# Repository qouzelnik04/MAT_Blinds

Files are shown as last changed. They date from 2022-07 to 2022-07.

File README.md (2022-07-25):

# MAT_Blinds

## Introduction
- hardware has revision (rev)
- software has version (ver)

Fully automatic blinds with the possibility of manual control. They allow setting the position of the blind, the pull up / pull down time. User interface with display and buttons. 
- constantly evolving project
- works with "day and night" blinds
- based on STM32
- whole instructions in the documentation

## News
Work is underway on [rev_2.0](./Schematic/rev_2.0/README.md), which should be released during July 2022.

features [rev_2.0](./Schematic/rev_2.0/README.md)
- custom PCB
    - universal PCB
- encoder/buttons
- support [ver_2.0](./Code/ver_2.0/README.md)
    - English menu
    - Encoder

## Video
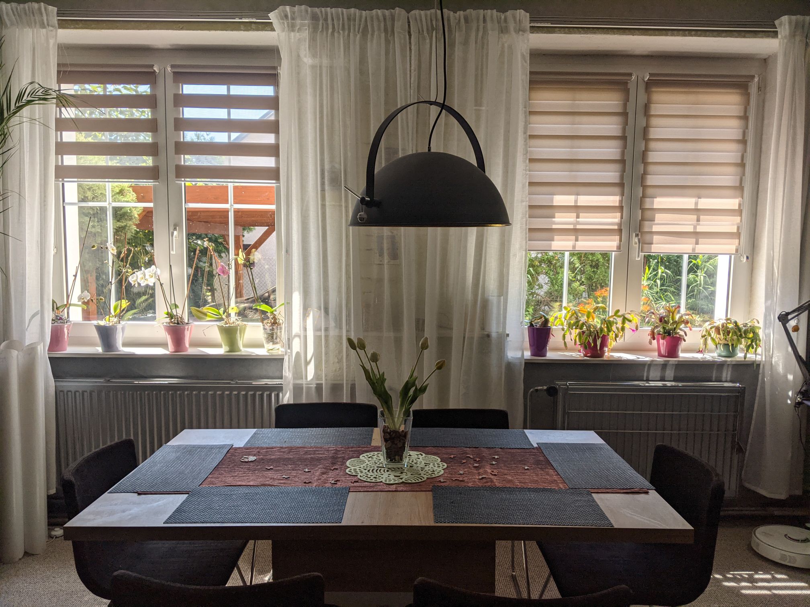
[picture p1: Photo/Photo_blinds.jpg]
(https://youtube.com/shorts/5kGoCTF1azA "Click to Watch!")

Click to Watch! ([rev_3.0](./Schematic/rev_3.0/) with [ver_3.0](./Code/ver_3.0/))

## Present
[rev_3.0](./Schematic/rev_3.0/) currently works with software [ver_3.0](./Code/ver_3.0/)

## Future improve
- release [rev_2.0](./Schematic/rev_2.0/README.md)
- release [ver_2.0](./Code/ver_2.0/README.md)
- lights sensors
- google assistant support

## Documentation
- [Instructions](./explanations/instructions.md)
- [Scheamtic](./Schematic/)
- [Code](./Code/)
- [Photo](./Photo/)

## License
Licensed under the [MIT License](./LICENSE)

## Author
- [@qouzelnik04](https://www.github.com/qouzelnik04)

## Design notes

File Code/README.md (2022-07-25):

# Software

## Introduction
- hardware has revision ([rev](../Schematic/README.md))
- software has version ([ver](./README.md))

For each software version, it is written which board revision it supports. This must be observed.
Each version of the software has detailed specifications of what it supports in the "README.md" file.

The software versions, their advantages and disadvantages are listed below.

## Actual version
### [ver_1.1](./ver_1.1/README.md) (not recommended)
- advantages
    - support 6 blinds
    - automatic pulling up and pulling down
- disadvantages
    - Required knowledge of STM32Cube to calibrate the blind.
    - support only Czech

### [ver_3.0](./ver_3.0/README.md) (recommended)
- advantages
    - easy to build (support [rev_3.0](../Schematic/rev_3.0/README.md))
    - support 4 blinds
    - automatic pulling up and pulling down
    - Supports English and Czech languages.

## Coming Soon
### [ver_2.0](./ver_2.0/README.md)
- advantages
    - Supports English and Czech languages.
    - support 6 blinds
    - automatic pulling up and pulling down
    - ...

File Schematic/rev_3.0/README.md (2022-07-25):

# rev_3.0 

## Introduction
rev_3.0 is the hardware part of the MAT_Blinds project. It was launched during July 2022 and replaced [rev_1.0](../rev_1.0/README.md).

- Easy to build
- Supports software versions only from 3.0 ([ver_3.0](../../Code/ver_3.0/README.md))
- Up to 4 blinds (4 motors)
- 1.3" display with encoder 

## Parts
- NUCLEO-F411RE (MCU)
- Arduino CNC shield
- 4x A4988 (Stepper Motor Driver)
- SSH1106 (1.3" OLED display)
- Encoder
- Power supply (9V 1A)
- [Case](../../parts/3D_parts/Case_rev_3.0.obj) Big a shout-out to [my brother](https://www.instagram.com/matalan09/?theme=dark) for designing these proposals.

- [How to make rev_3.0 board](./How_to_make_board.md)

## Photo
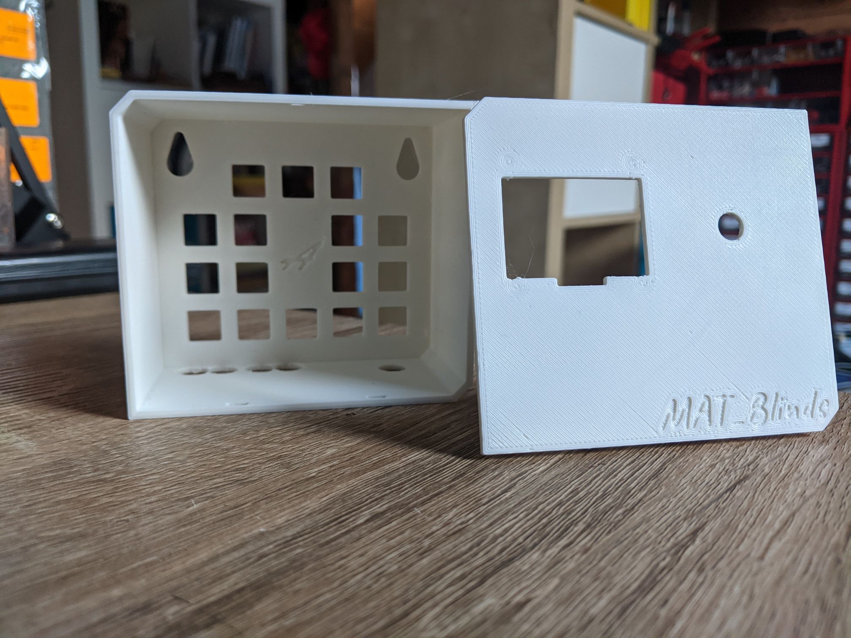
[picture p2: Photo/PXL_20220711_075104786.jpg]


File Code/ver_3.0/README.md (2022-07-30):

# ver_3.0 

## Introduction
ver_3.0 is the software part of the MAT_Blinds project. It was launched during July 2022 and replaced [ver_1.0](../ver_1.0/README.md).

- Supports hardware versions only 3.0 ([rev_3.0](..//../Schematic/rev_3.0/README.md))
- Supports English and Czech languages.
- easy to build (support [rev_3.0](../Schematic/rev_3.0/README.md))
- up to 4 blinds (4 motors)
    - the blinds are pulling up / pulling down at the same time
    - [separate control](../../explanations/separate_control.md)   
- 1.3" display with Encoder

### Update for version 3.1
- ver_3.1
    - code optimization
    - larger range of blinds
    - greater accuracy of blinds
    - add display shutdown after 30s of non-use

Here is [Setup](Setup.md) 

## Video
(https://youtube.com/shorts/5kGoCTF1azA "Click to Watch!")
Click to Watch! ([rev_3.0](./Schematic/rev_3.0/) with [ver_3.0](./Code/ver_3.0/))

## Photo
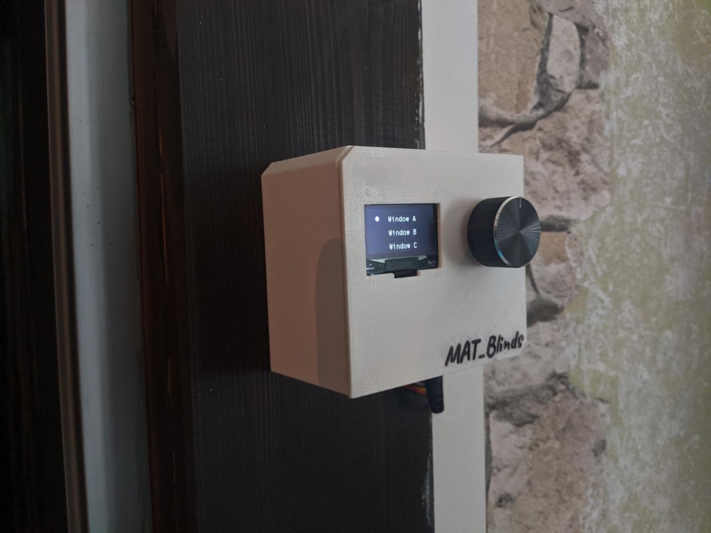
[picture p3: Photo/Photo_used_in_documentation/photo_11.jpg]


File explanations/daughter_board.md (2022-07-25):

# Daughter board

## Introduction
An explanation of what "daughter board" means.

Daughter boards are printed circuit boards with a required chip mounted on them with few other hardware components. 
## Examples of photos
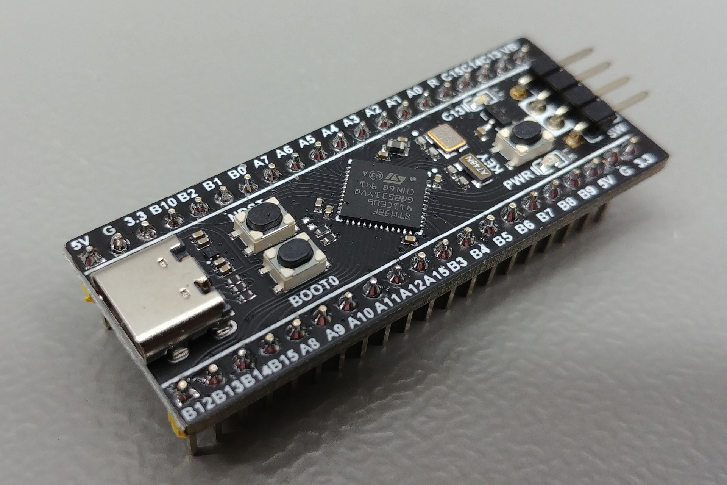
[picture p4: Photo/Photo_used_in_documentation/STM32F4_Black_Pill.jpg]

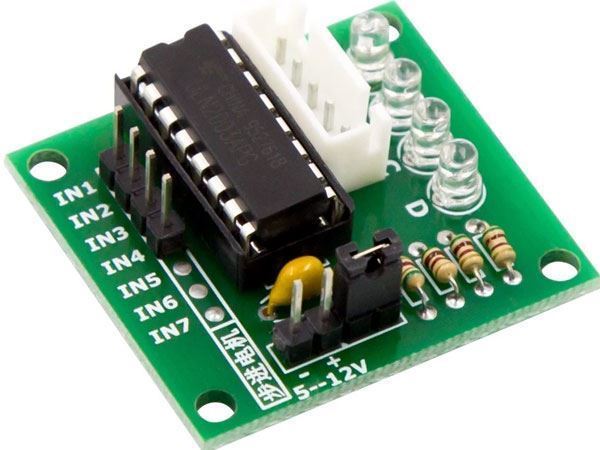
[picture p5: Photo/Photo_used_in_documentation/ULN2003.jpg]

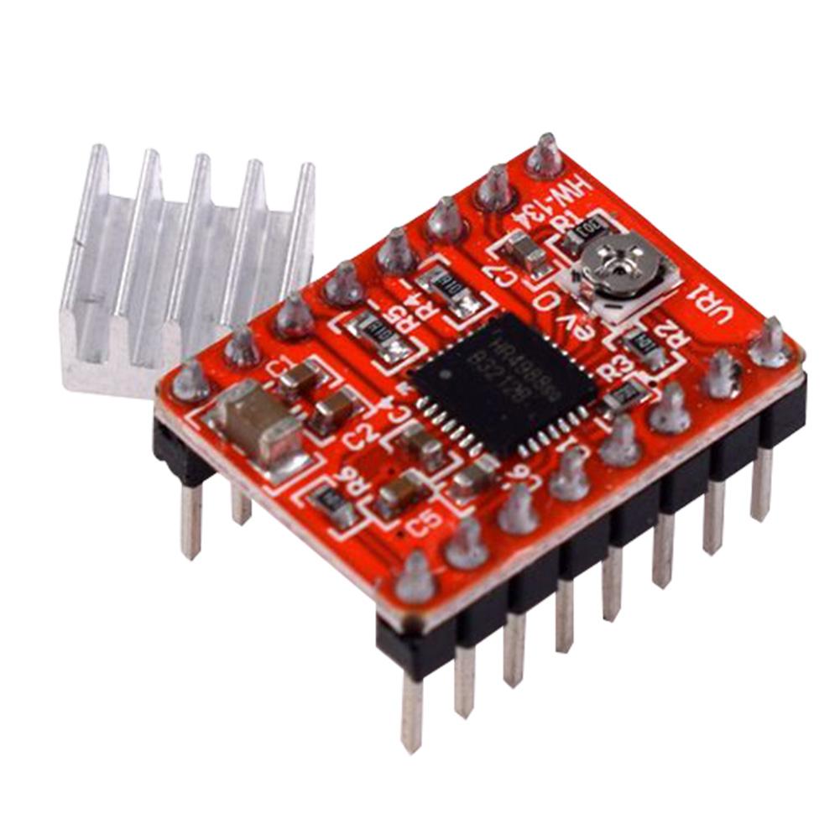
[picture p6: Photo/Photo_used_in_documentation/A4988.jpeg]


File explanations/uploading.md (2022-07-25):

# Uploading

## STM32 ST-LINK utility
### requirements 
- ST Link (if you have [revision 3.0](../Schematic/rev_3.0/)) it already has ST-Link built into it.
- [STM32 ST-LINK utility](https://www.st.com/en/development-tools/stsw-link004.html#get-software)

After downloading the STM32 ST-LINK utility and opening it, you will get [here](../Photo/Photo_used_in_documentation/ST_LINK_utility_3.png).

Now we connect the board to the computer. 
- If we have revision 3.0, it will be much easier, we will only need a mini USB cable.
- If we have revision 1.0, dirstly we will need to connect the board to ST-Link and ST-Link to the computer. [As in the picture](../Photo/Photo_used_in_documentation/ST_LINK_utility_4.jpg)
    - yellow - SWDIO
    - blue - GND
    - green - SWCLK
    - orange -3.3V
- Now we will download the software. In the folder of the software version we want to use, there is a file called ver_x.x.hex, for example (ver_3.0.hex). We'll download it.
- Now we connect the board in the STM32 ST-Link utility, by clicking on the "Connect to the target" button. If the board connects successfully, below we see the name of the board and it is connected. [As in the picture](../Photo/Photo_used_in_documentation/ST_LINK_utility_5.png)
- Now drag the downloaded .hex file into the STM32 ST-Link utility and click on "Program verify" then click on start. Then it should write something similar to the [picture](../Photo/Photo_used_in_documentation/ST_LINK_utility_7.png)
- Now the software is uploaded, all we have to do is disconnect from the device by clicking "Disconnect form the target" [As in the picture](../Photo/Photo_used_in_documentation/ST_LINK_utility_9.png)

### Photo

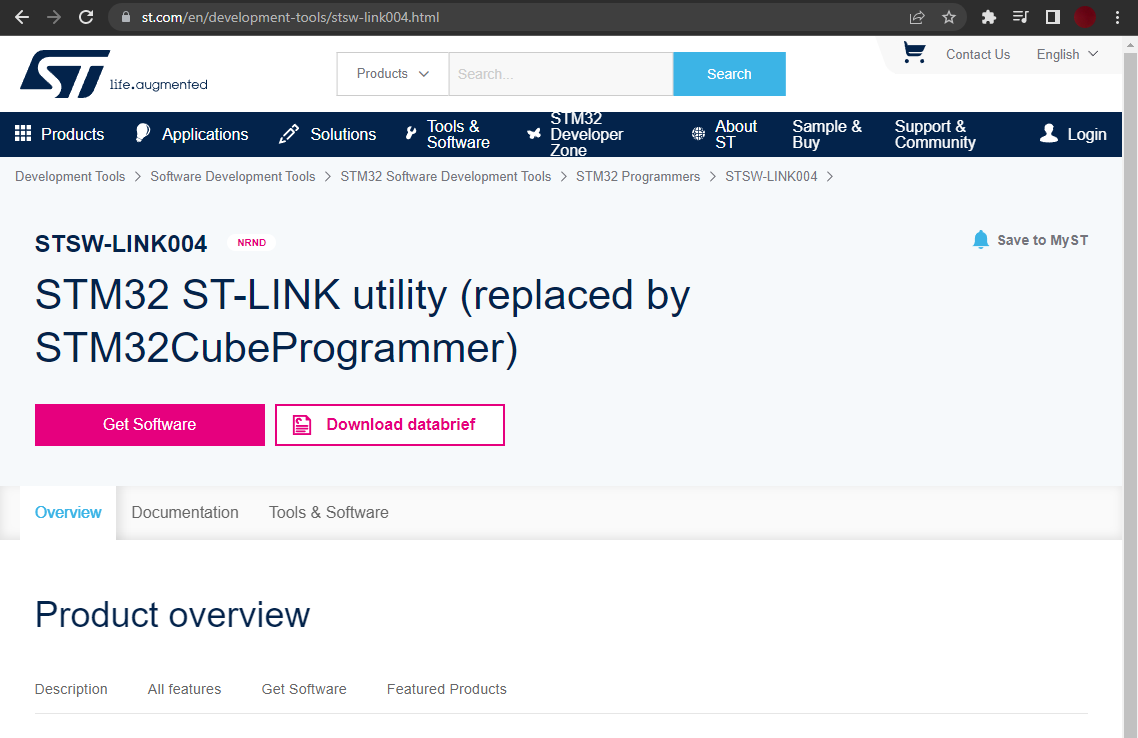
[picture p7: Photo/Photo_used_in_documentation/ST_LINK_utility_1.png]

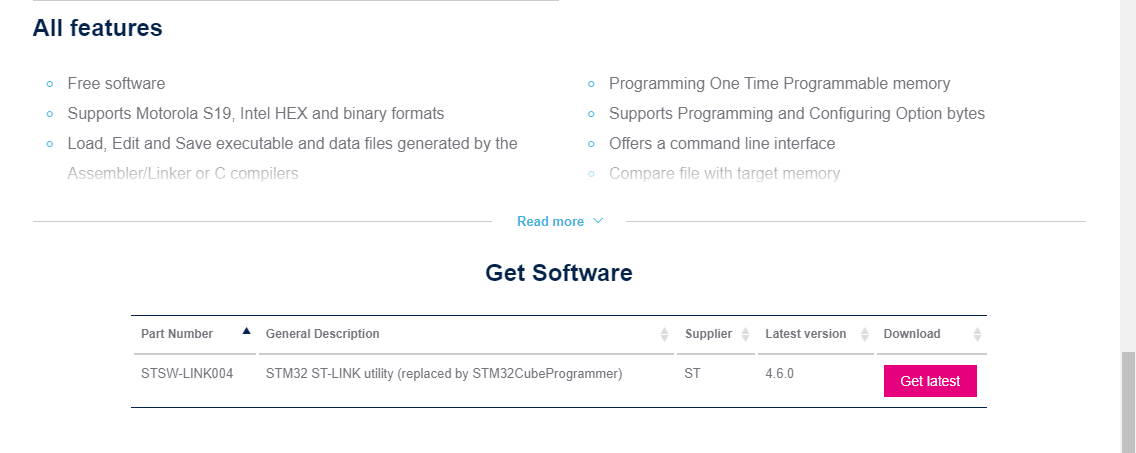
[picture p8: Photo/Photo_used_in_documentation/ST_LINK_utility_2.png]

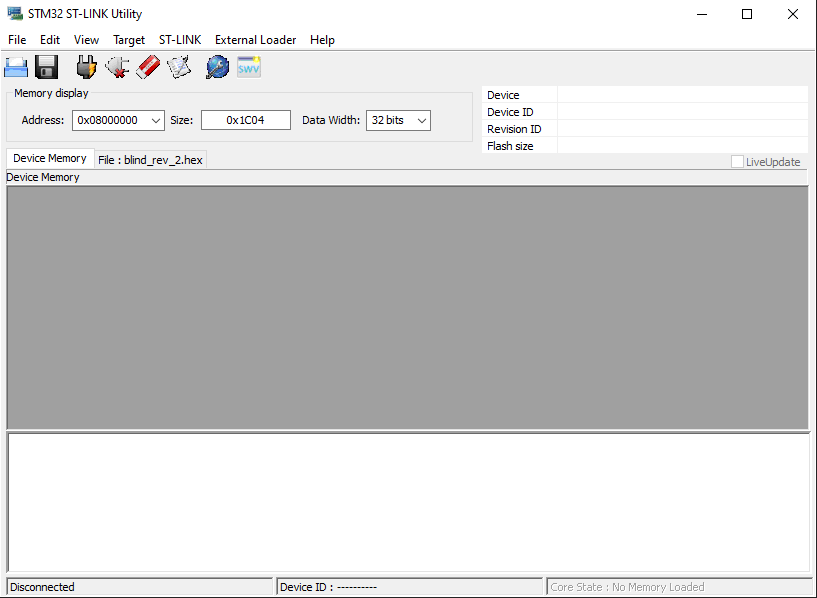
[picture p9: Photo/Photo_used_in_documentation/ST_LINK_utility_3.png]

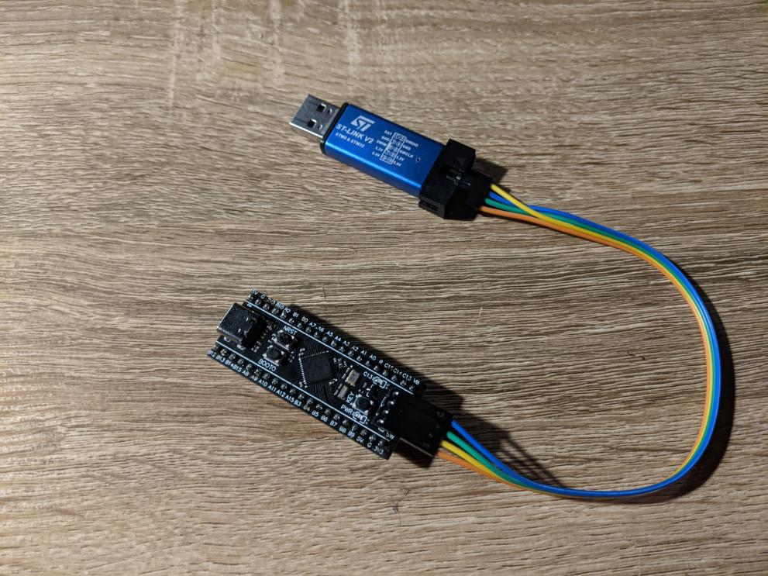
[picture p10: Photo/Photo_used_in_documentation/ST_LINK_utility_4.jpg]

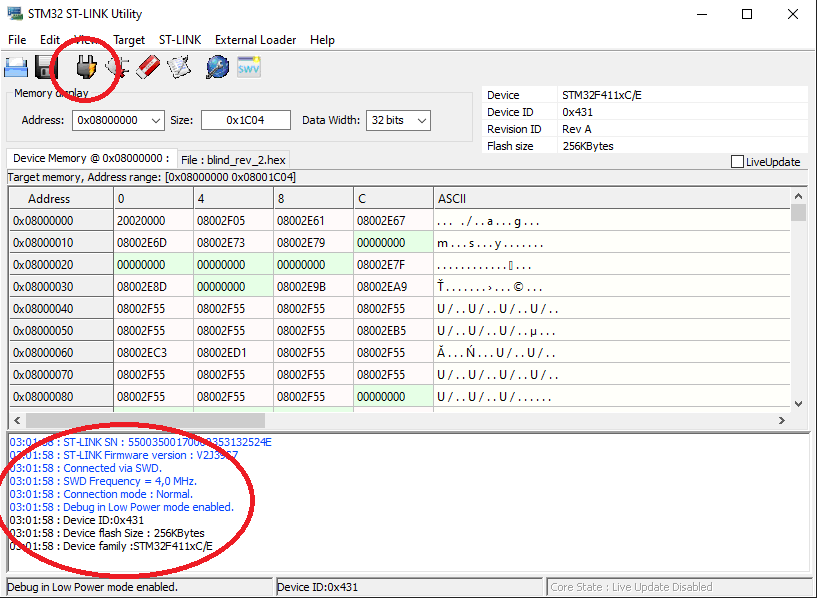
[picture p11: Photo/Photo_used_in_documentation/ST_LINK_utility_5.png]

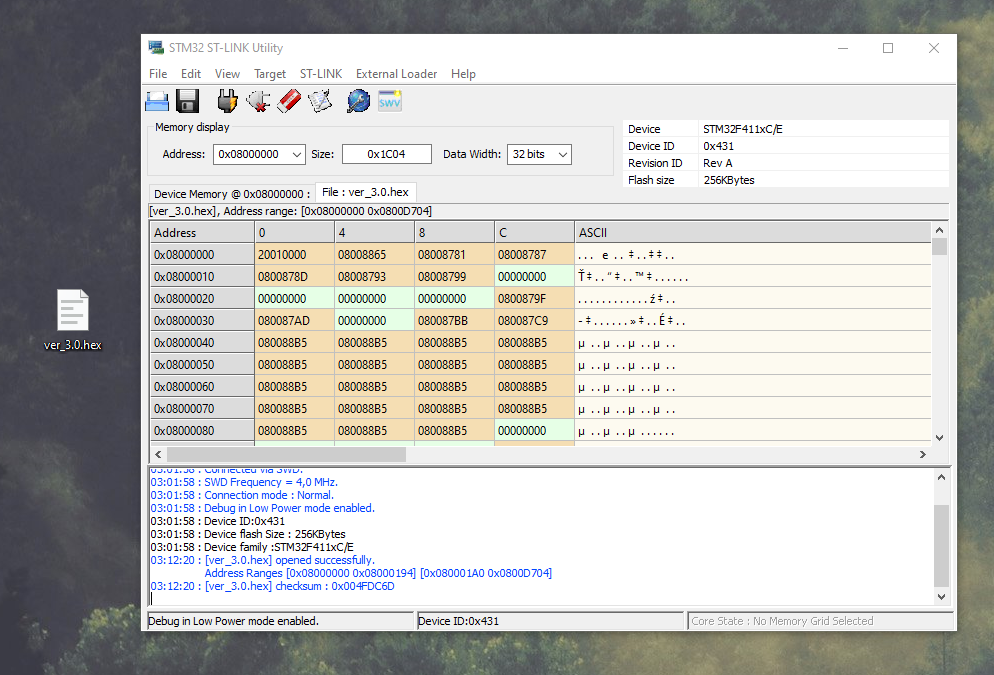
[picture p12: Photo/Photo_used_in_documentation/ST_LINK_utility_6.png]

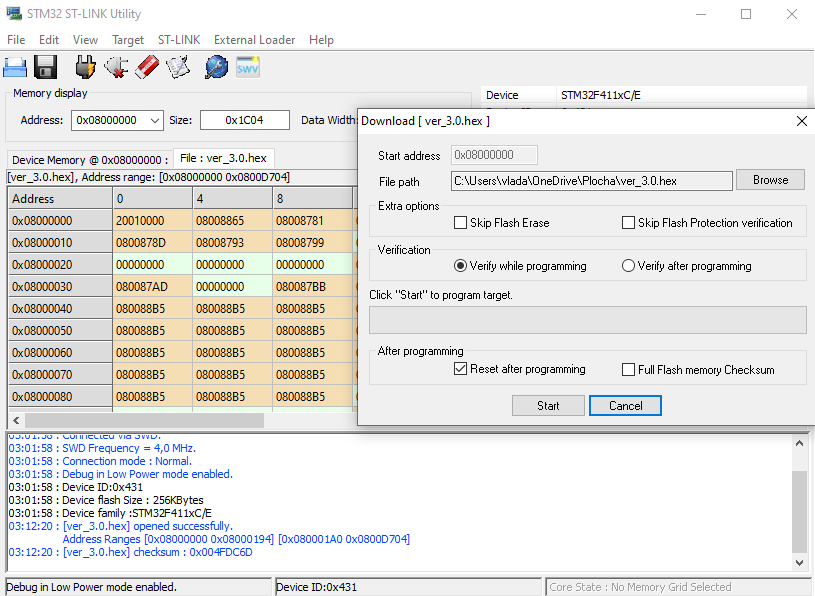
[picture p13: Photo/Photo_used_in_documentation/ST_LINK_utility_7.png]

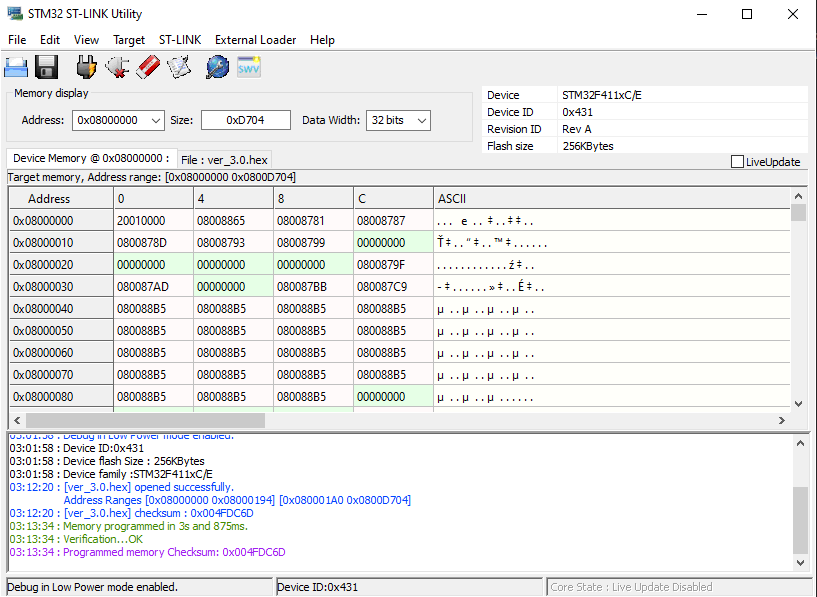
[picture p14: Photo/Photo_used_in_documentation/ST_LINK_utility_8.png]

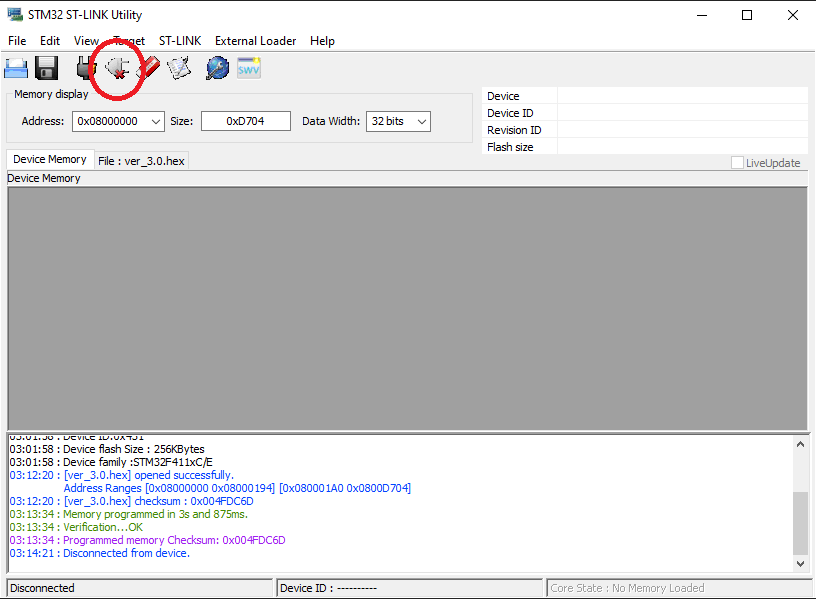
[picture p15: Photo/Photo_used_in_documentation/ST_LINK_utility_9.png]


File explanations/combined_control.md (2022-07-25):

# Combined control

## Introduction
blind position window_A = blind position window_A_2, same for B and C

## Photo
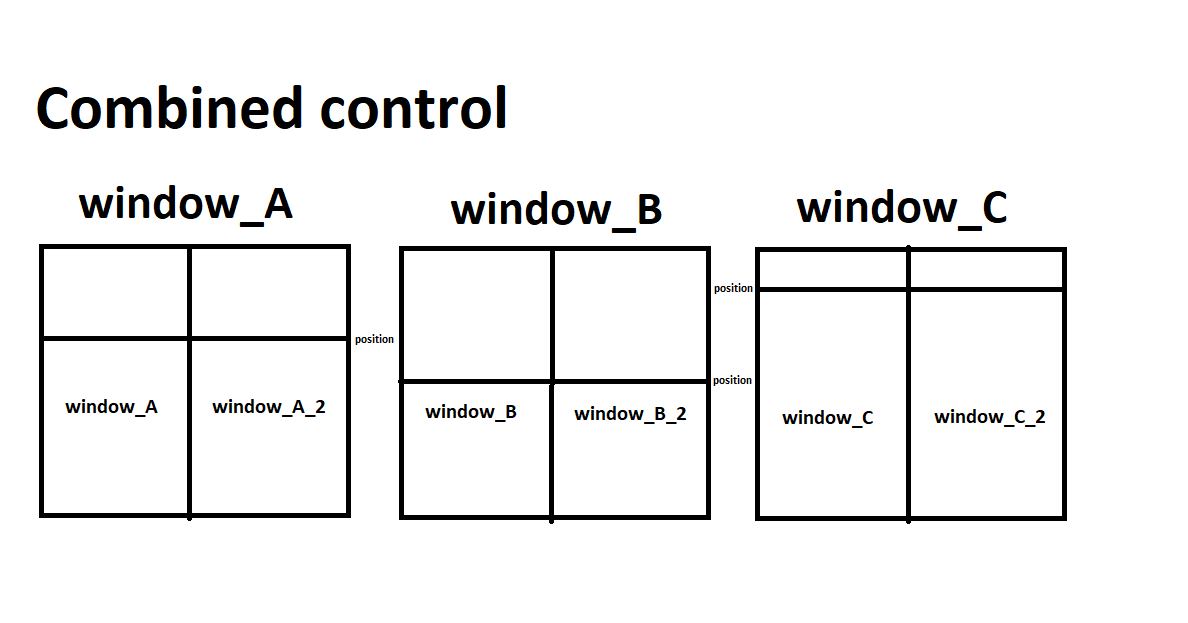
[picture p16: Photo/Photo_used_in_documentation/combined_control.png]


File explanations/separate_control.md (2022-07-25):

# Separated control

## Introduction
the position of the window_A blind does not have to be equal with the position of the window_A_2 blind, but it can, same for B and C.
## Photo
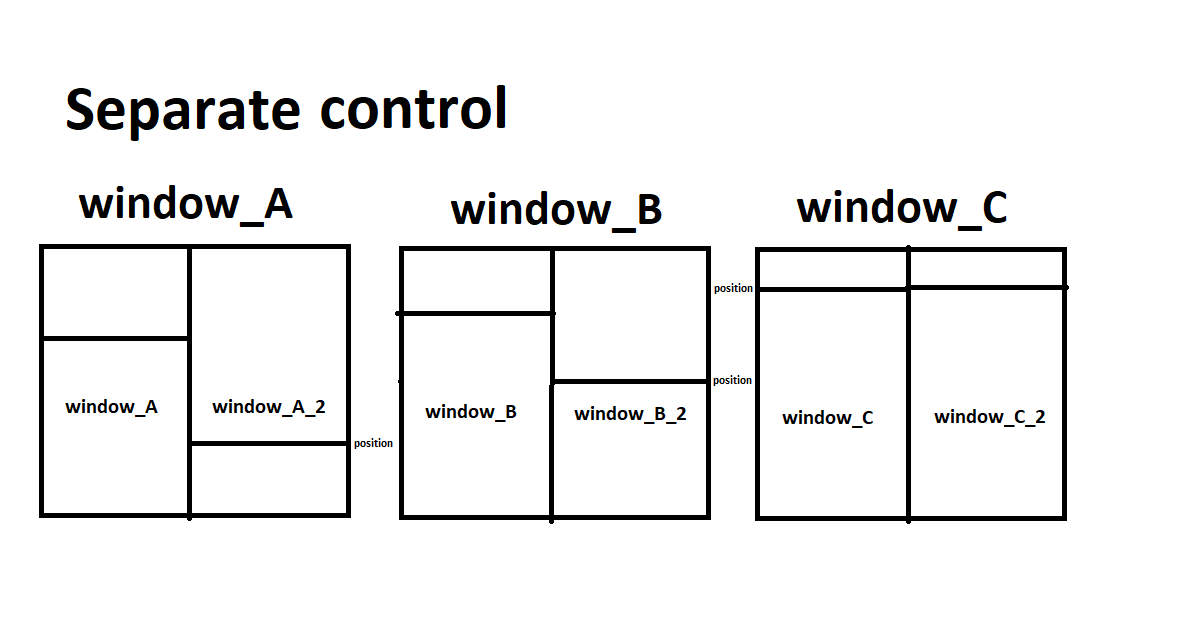
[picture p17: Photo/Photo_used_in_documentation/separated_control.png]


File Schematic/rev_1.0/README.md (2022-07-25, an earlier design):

# rev_1.0

## Introduction
rev_1.0 is the hardware part of the MAT_Blinds project. It was launched in early May and was permanently replaced by [rev_3.0](../rev_3.0/README.md) in July 2022. 

- It only supports software versions up to 1.1 ([ver_1.1](../../Code/ver_1.1/README.md)).
- Up to 6 blinds (6 motors)
- 1.3" display with 3 buttons
- Complete [Schematic](./Schematic.pdf)

## Parts
- STM32F401 (MCU, Development Board)
    - [Pinout](../../Photo/Photo_used_in_documentation/rev_1.0_STM32_Pinout.png)
- 6x ULN2003 (Stepper Motor Driver Board)
- SSH1106 (1.3" OLED display)
- LD33V (3.3V LDO Regulator)
- Power supply (9V 1.5A)

## Photo
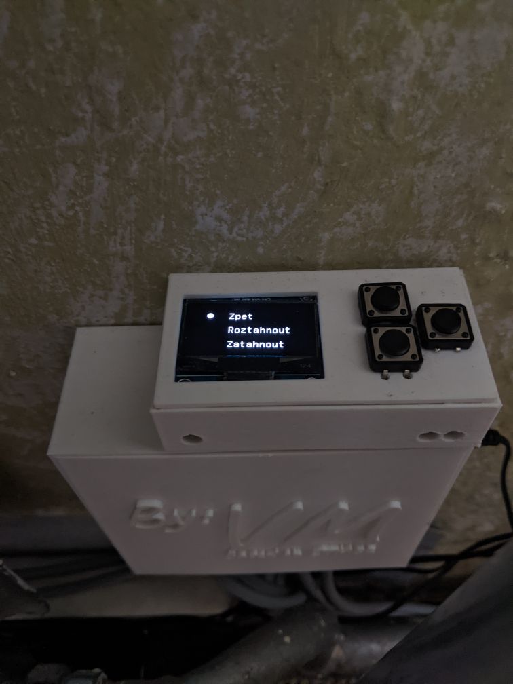
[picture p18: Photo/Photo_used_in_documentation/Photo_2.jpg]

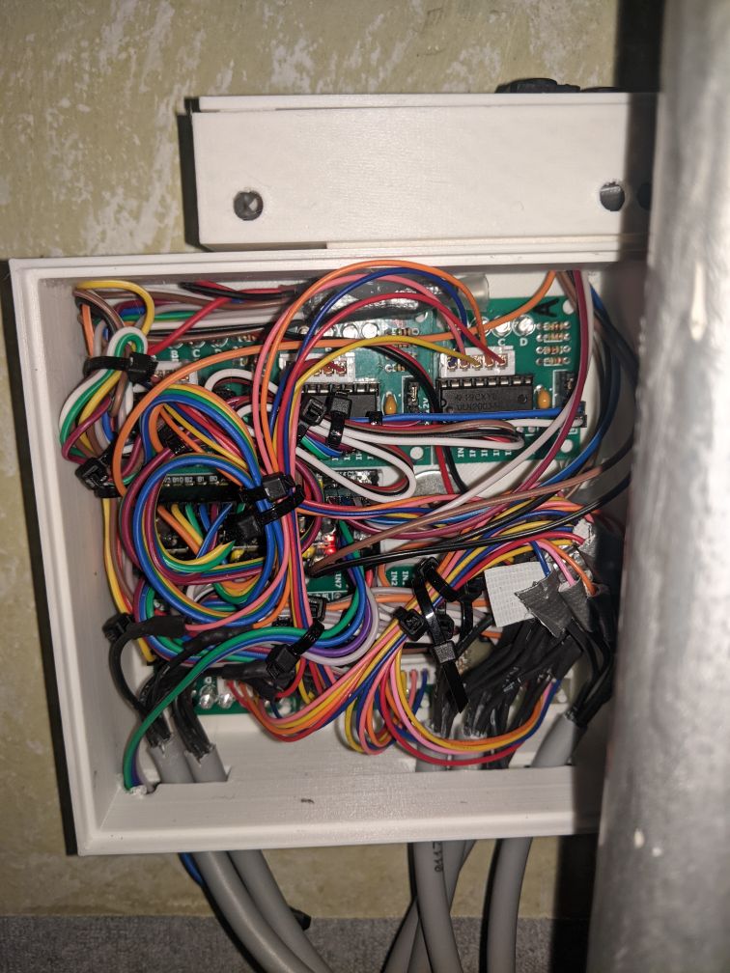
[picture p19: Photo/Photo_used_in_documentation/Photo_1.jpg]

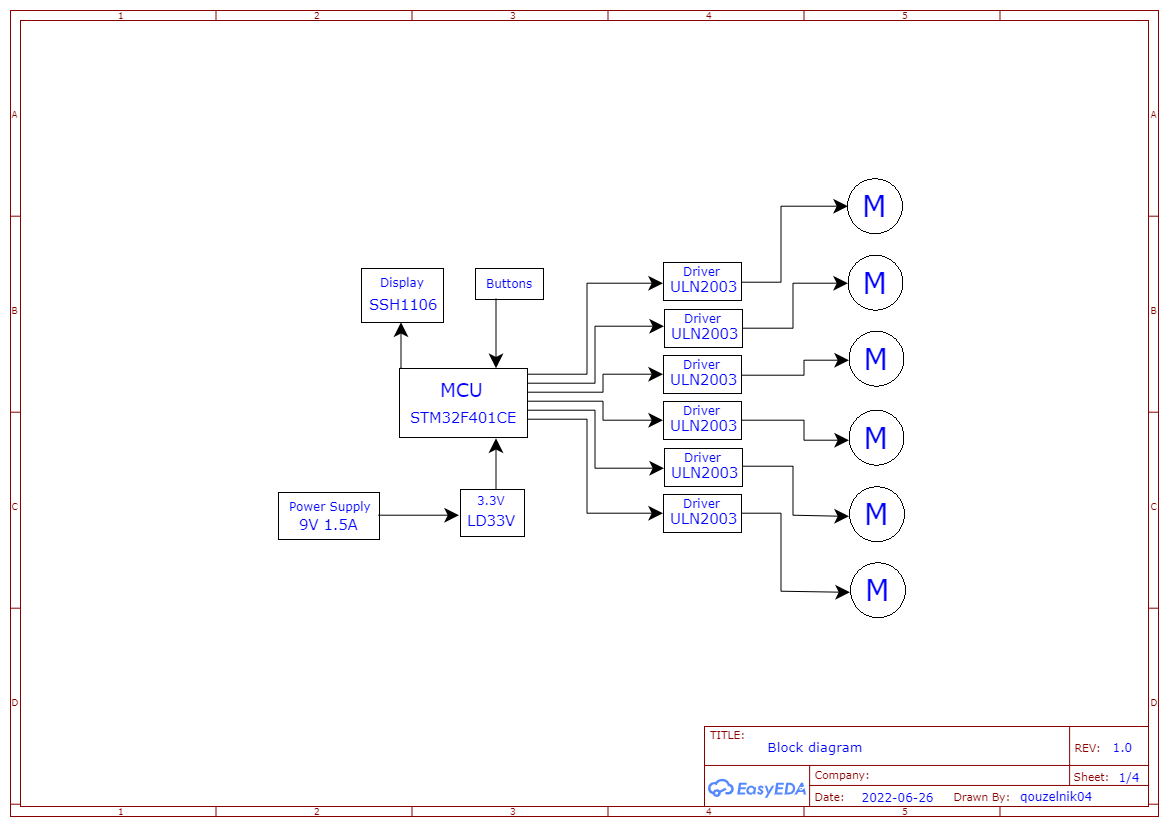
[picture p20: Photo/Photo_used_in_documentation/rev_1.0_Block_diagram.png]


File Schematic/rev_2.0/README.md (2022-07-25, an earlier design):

# rev_2.0 coming soon

## Introduction
rev_2.0 is the hardware part of the MAT_Blinds project. It should be launched during 2022.

- Supports software versions only from 2.0 ([ver_2.0](..//../Code/ver_2.0/README.md))
- up to 6 blinds (6 motors)
- 1.3" display with encoder or 3 buttons 
- support up to 4 light sensors
- support WiFi connection

## Parts
- STM32F401 (MCU)
    - [Pinout](../../Photo/Photo_used_in_documentation/rev_2.0_STM32_Pinout.png)
- ESP-12E (MCU)
- 6x A4988 (Stepper Motor Driver)
- SSH1106 (1.3" OLED display)
- AMS1117-3.3 (3.3V LDO Regulator)
- power supply (9V 1.5A)

## Photo
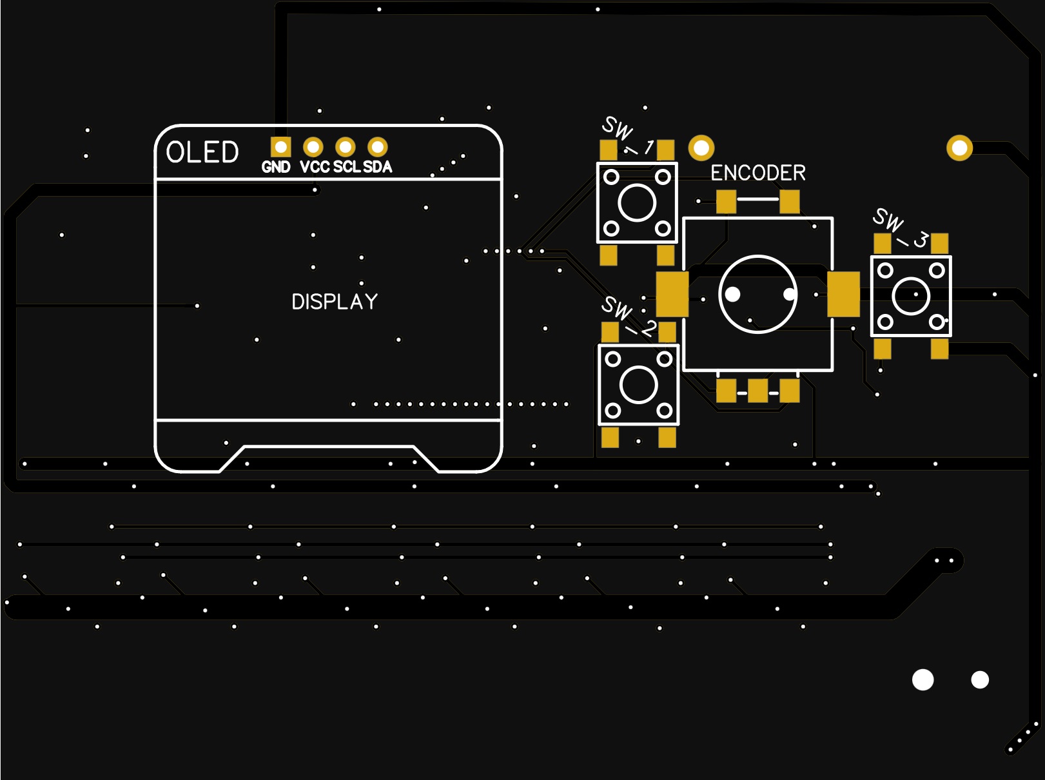
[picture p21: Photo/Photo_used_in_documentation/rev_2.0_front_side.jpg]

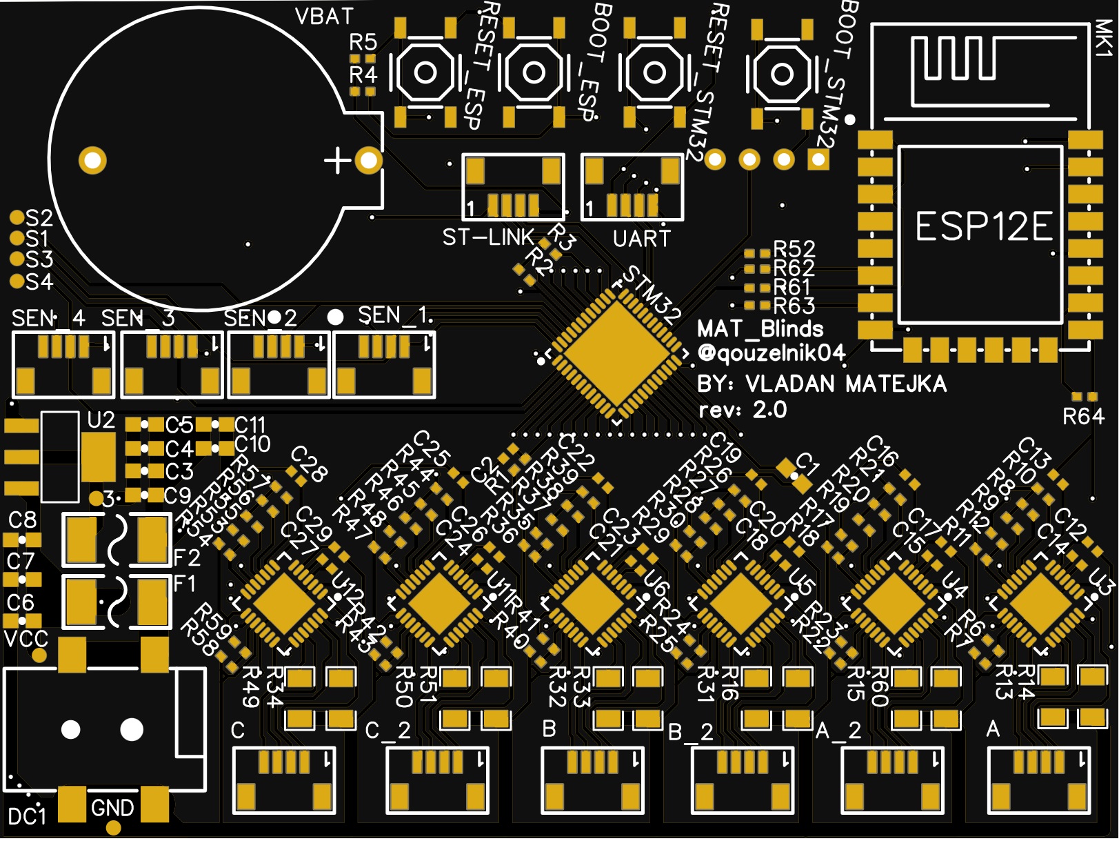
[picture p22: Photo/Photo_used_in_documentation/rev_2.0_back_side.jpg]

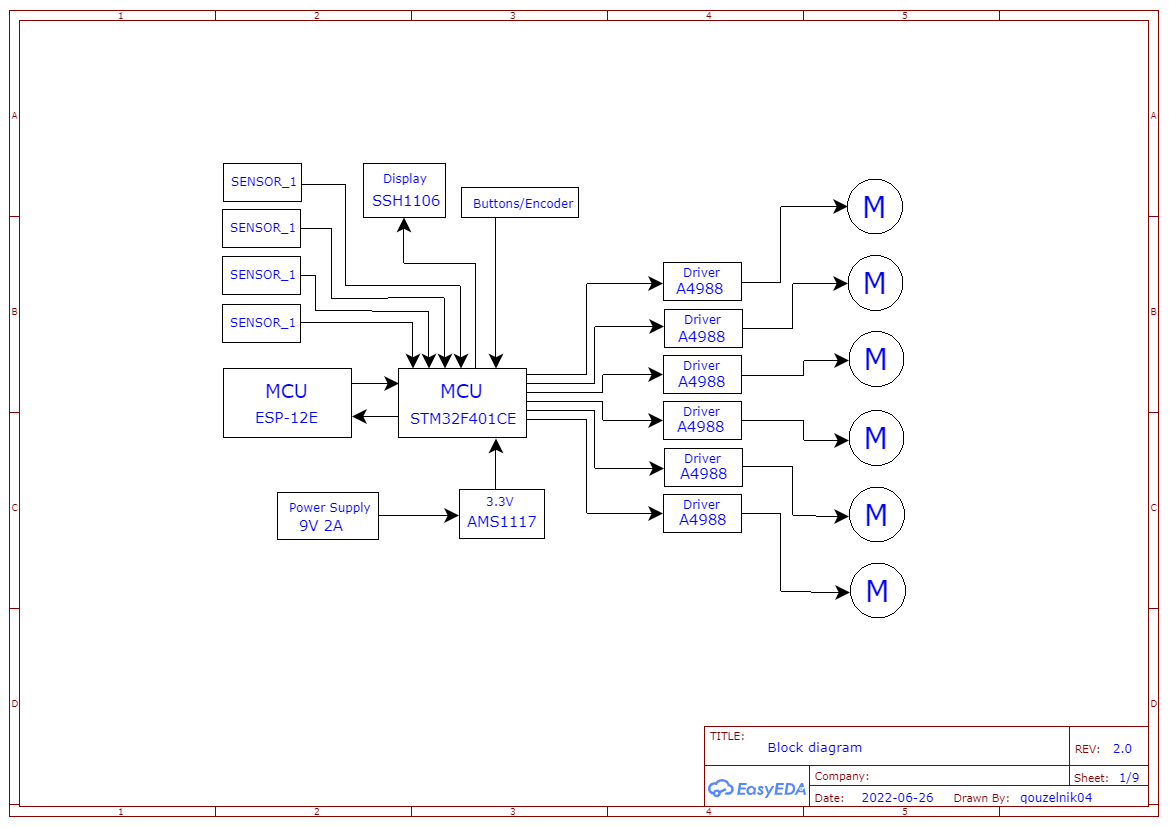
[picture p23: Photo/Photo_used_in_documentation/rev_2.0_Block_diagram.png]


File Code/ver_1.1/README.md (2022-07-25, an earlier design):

# ver_1.1

## Introduction
ver_1.1 is the software part of the MAT_Blinds project. It was launched in early May 2022 and should be permanently replaced by [ver_2.0](../ver_2.0/README.md) in July 2022. 

- It only supports hardware revision 1.0 ([rev_1.0](../../Schematic/rev_1.0/README.md))
- only Czech language supported
- up to 6 blinds (6 motors)
    - the blinds are retracted / extended one after the other
    - [combined control](../../explanations/combined_control.md) - blind position window_A = blind position window_A_2, same for B and C
- 1.3" display with 3 buttons

- disadvantages
    - Required knowledge of STM32Cube to calibrate the blind.
    - support only Czech

Here is [Setup](Setup.md) 

## Photo


## Video
(https://www.youtube.com/watch?v=2pDpsi7qXGo "Click to Watch!")
Click to Watch! ([rev_1.0](./Schematic/rev_1.0/) with [ver_1.1](./Code/ver_1.1/))

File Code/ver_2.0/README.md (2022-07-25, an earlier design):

# ver_2.0 coming soon

## Introduction
ver_2.0 is the software part of the MAT_Blinds project. It should be launched during 2022.

- Supports hardware versions only from 2.0 ([rev_2.0](..//../Schematic/rev_2.0/README.md))
- Supports English and Czech languages.
- up to 6 blinds (6 motors)
    - the blinds are pulling up / pulling down at the same time
    - possibility of [combined control](../../explanations/combined_control.md) or [separate control](../../explanations/separate_control.md)   
- 1.3" display with Encoder

## Photo

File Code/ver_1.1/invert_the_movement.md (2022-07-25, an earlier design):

# How to invert the movement of the blind

## Introduction
If we need to invert the movement of the blind. In STM32Cube, in "main.c" using the "ctrl+f" function, we search for "TODO" and in the "motor_action" function, we have to change the value in the cell of the "stepper_step_angle" function, from 1 to 0 or from 0 to 1. It is always written "TODO".

### Photo
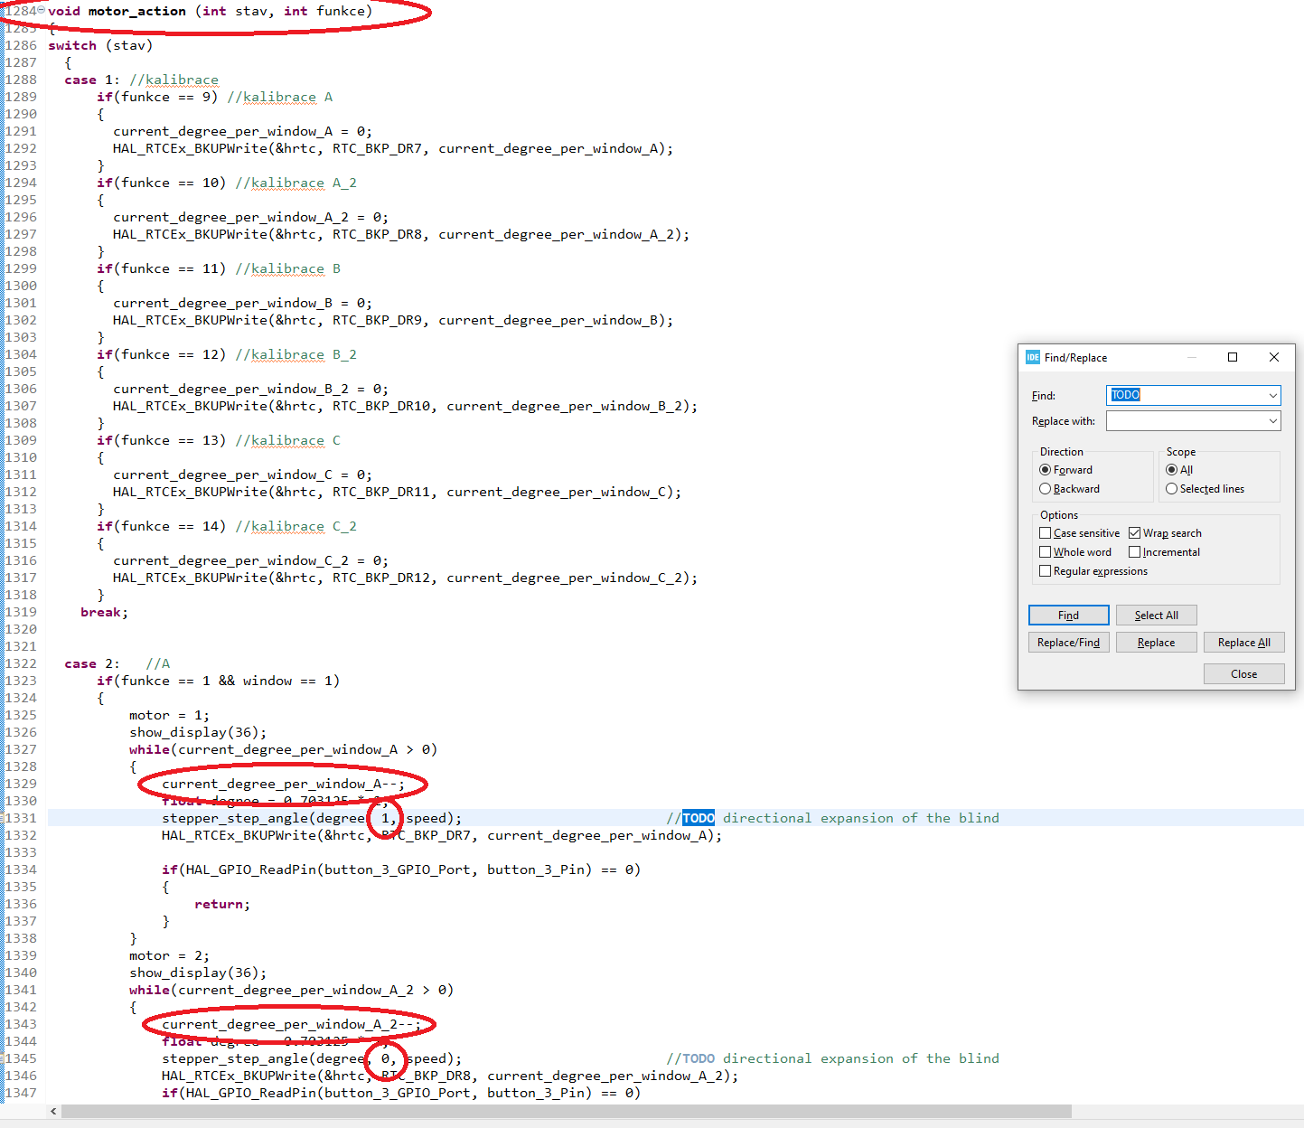
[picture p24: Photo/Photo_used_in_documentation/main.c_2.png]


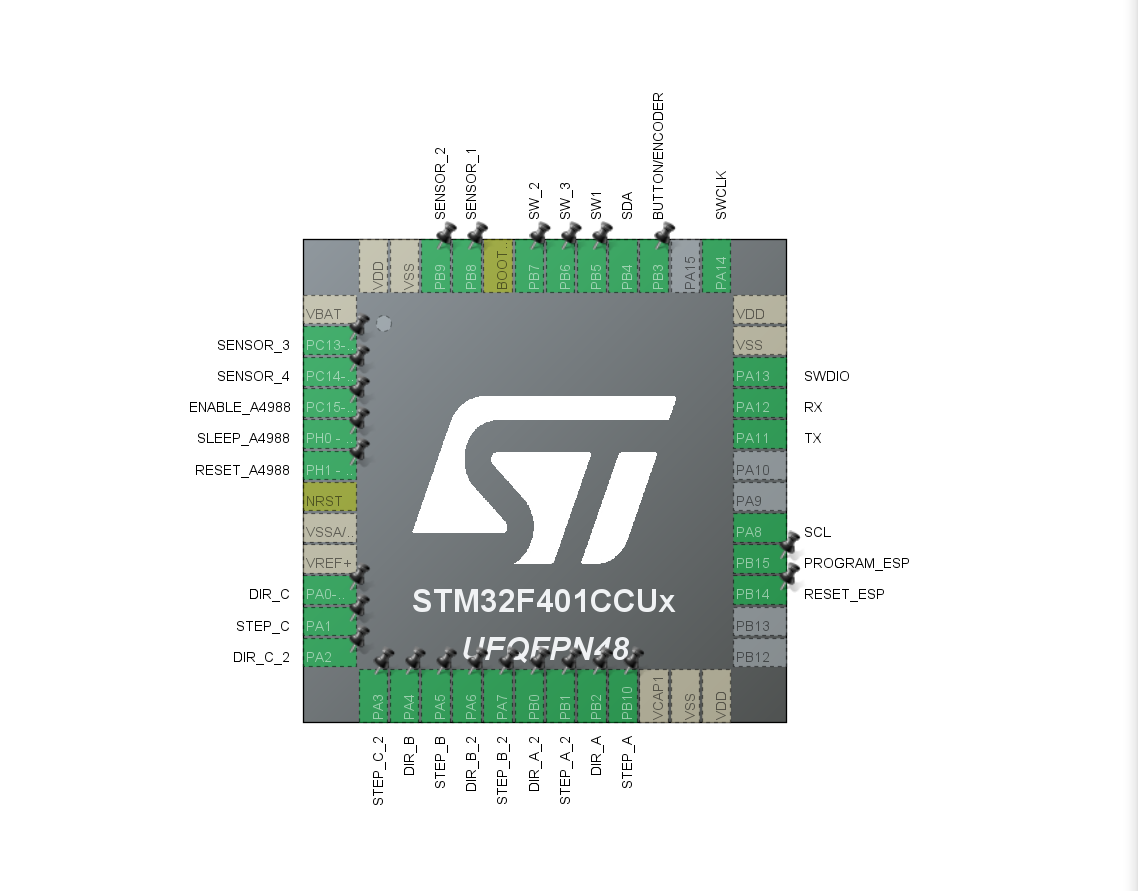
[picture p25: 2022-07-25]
Photo/Photo_used_in_documentation/rev_2.0_STM32_Pinout.png

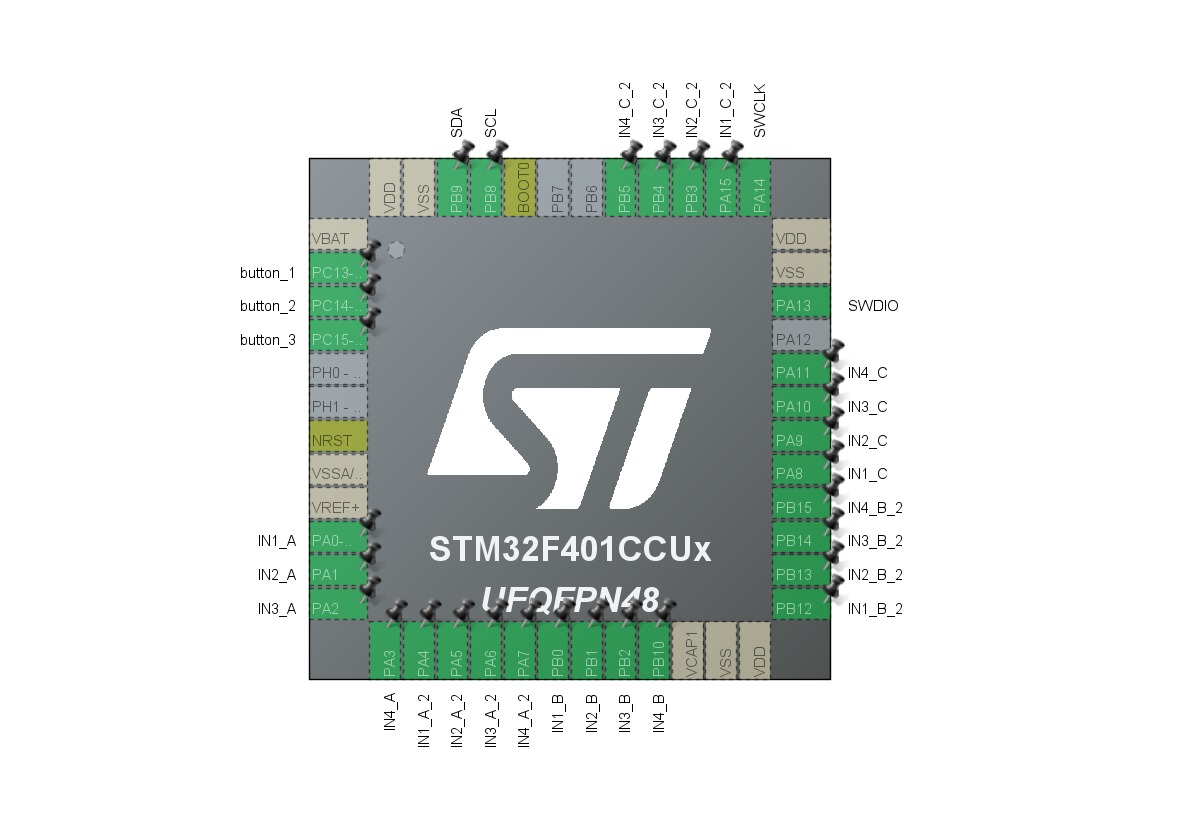
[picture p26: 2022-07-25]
Photo/Photo_used_in_documentation/rev_1.0_STM32_Pinout.png

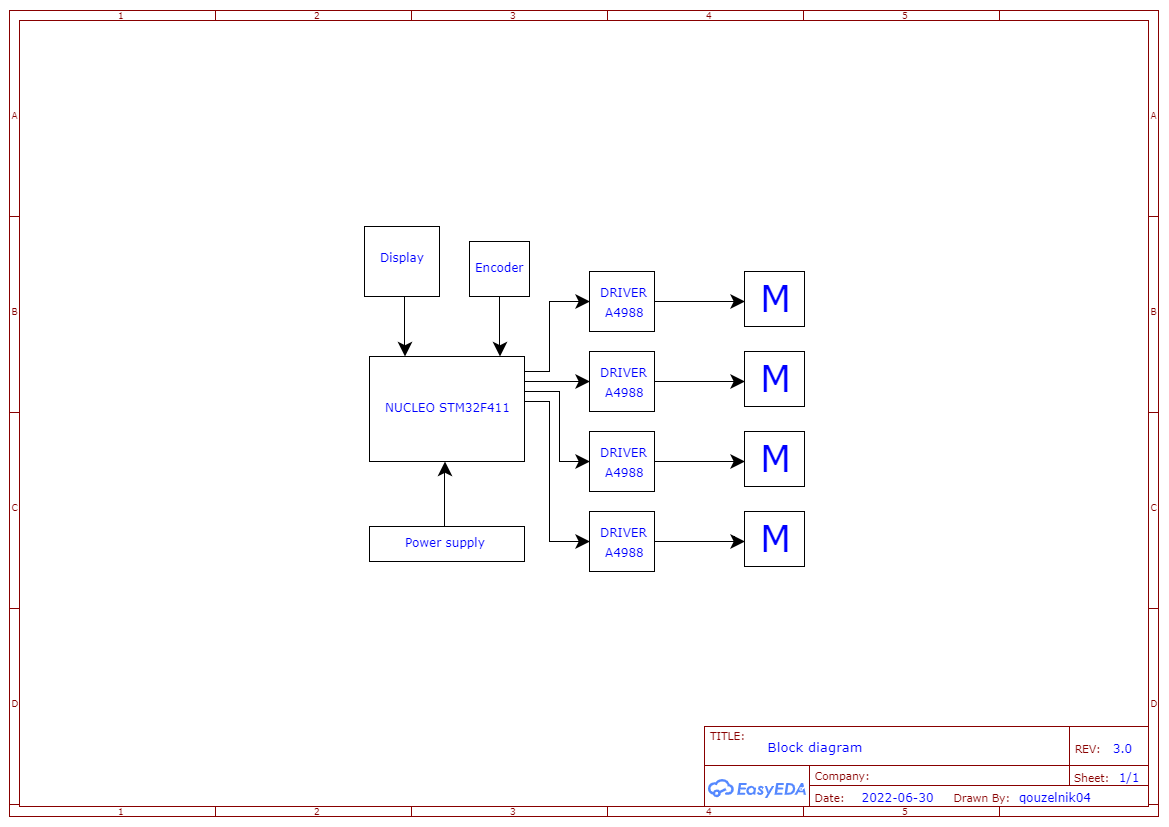
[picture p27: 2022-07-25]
Schematic/rev_3.0/rev_3.0_Block_diagram.png

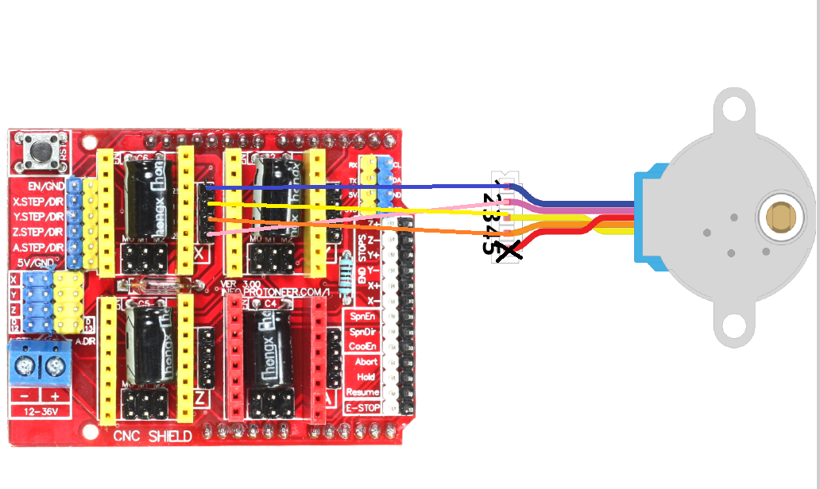
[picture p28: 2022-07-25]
Photo/Photo_used_in_documentation/Connect_motor_CNC.png

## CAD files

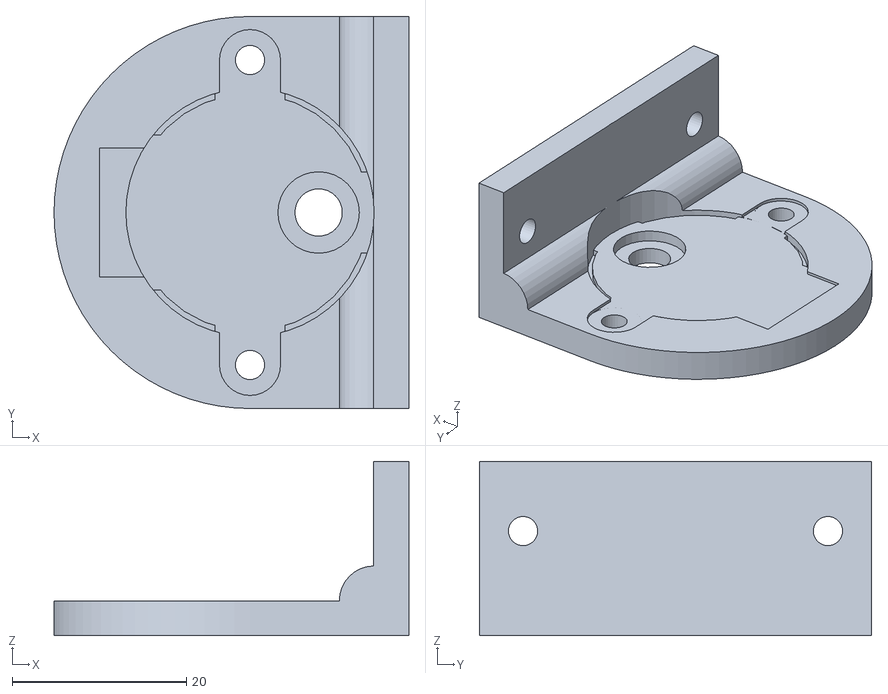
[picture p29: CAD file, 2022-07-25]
parts/3D_parts/Bracket_28BYJ-48_v1.stl
40.8 x 45.0 x 20.0

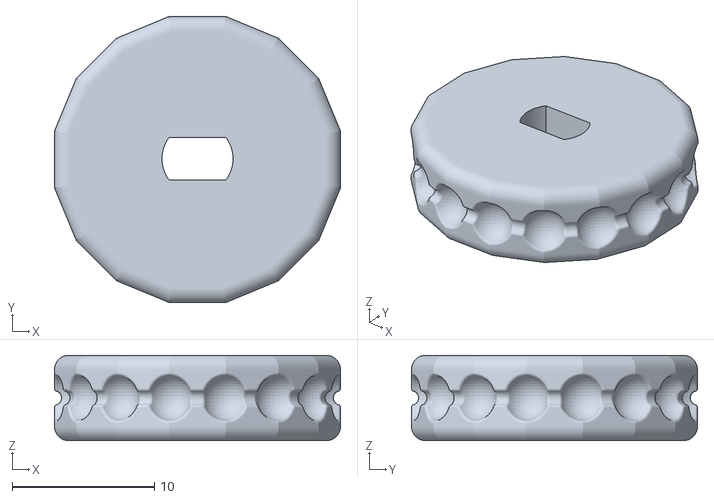
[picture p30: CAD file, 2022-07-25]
parts/3D_parts/Drive_wheel/Drive_Wheel.stl
20.1 x 20.1 x 6.00

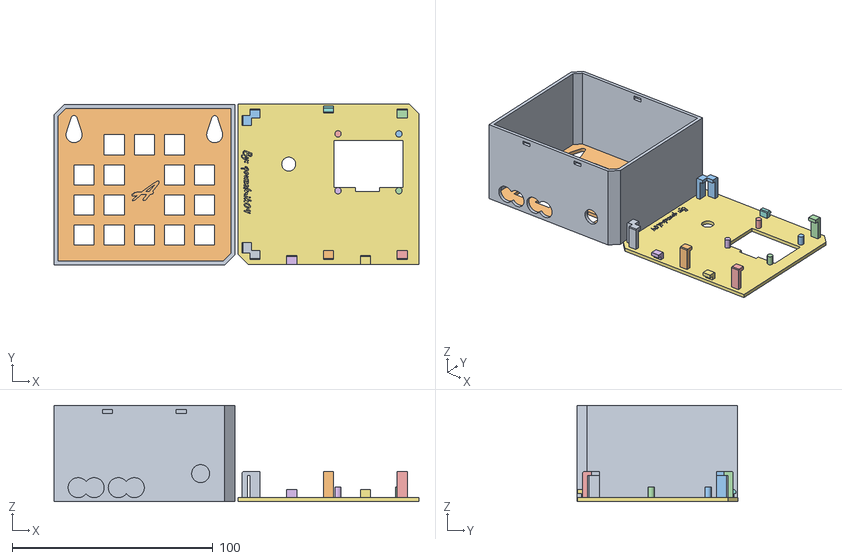
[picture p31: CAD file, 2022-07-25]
parts/3D_parts/Case_rev_3.0.obj
181.7 x 80.4 x 48.0

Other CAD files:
parts/3D_parts/Drive_wheel/Drive_Wheel_4.5mm_beads.stl

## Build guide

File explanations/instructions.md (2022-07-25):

# Instructions

## Introduction
Here ARE complete instructions for installation and using of MAT_Blinds.

## Basic concepts
- hardware has revision ([rev](../Schematic/))
    - hardware revision = board revision
- software has version ([ver](../Code/))

## Step 1 (choose software)
You will need to select the [software](../Code/) you want to use and choose the [board revision](../Schematic/) that the software supports. (For each software version, it is written which board revision it supports.)

## Step 2 (parts)
You will needs to print a few parts on a 3D printer.
- [bracket for stepper motor](../parts/3D_parts/Bracket_28BYJ-48_v1.stl) Big a shout-out to [John Beale](https://www.thingiverse.com/jbeale/designs) for this proposal.  (only for 28BJY-48)
- [drive wheel](../parts/3D_parts/Drive_wheel/) Big a shout-out to [Martin Bucknall](https://www.thingiverse.com/paraglider_nut/designs) for designing these proposals. 
    - (Each type of blinds need a different one, according to the chain. I used these two because I have two different types of blinds.)

parts list
- 6x - stepper motor (I use [28BJY-48](../Schematic/datasheets/28BYJ-48.pdf))
- power supply - A recommended power supply is written for each [revision](../Schematic/).
- [board](../Schematic/) - which you selected in step 1.
- board case (not for every rev)
- self-tapping screws (for bracket mounting)

## Step 3 (create board)
After selecting the [software](../Code/) and correct [revision](../Schematic/) of the board. The board needs to be made. The entire schema is available for each board. (There are two ways how to make a board. The first one is to buy [daughter board](./daughter_board.md) and just connect them together according to the schema. The second option is to draw the board according to the schema and let them make.

## Step 4 (upload software)
So if we already have a board made, we will need to upload the software we want to use. There are more options for uploading software to the board. I chose the option using „STM32 ST-LINK Utility“ more about uploading [here](../explanations/uploading.md).

## Step 5 (setup board)
After uploading the software, you will still need to set up the board. Each software version has a file named Setup.md. According to it, you will set everything you need.

## Step 6 (congratulations)
If you get this far, the MAT_Blinds project should work for you at home. ❤

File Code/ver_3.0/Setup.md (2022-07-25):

# Setup 

## Introduction
- After the software is uploaded to the board, it still needs to be set up.

- We need to calibrate the blinds. First we go to (setup -> engines -> test). Now the blinds should go up, if not we press the button. We go to (settings -> engines) and here we click on Invert A/B/C/D according to which blind we need to invert. We go to (setup -> engines -> test) again and now all the blinds should be pulling up. If not, repeat the process, if yes, press the button again.

- Now we calibrate each blind. We go to (settings -> calibration) and here we will gradually calibrate each blind by clicking on the desired blind and then follow the instructions on the display.

- Now we just have to set the time in the settings and when we want to pull up / pull down the blinds.

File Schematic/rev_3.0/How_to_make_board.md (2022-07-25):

# How_to_make_board

## Introduction
This is a tutorial on how to make a board for rev_3.0.

## Parts
- NUCLEO-F411RE (MCU)
- Arduino CNC shield
- 4x A4988 (Stepper Motor Driver)
- SSH1106 (1.3" OLED display)
- Power supply (9V 1A)
    - connector for power supply
- [Case](../../parts/3D_parts/Case_rev_3.0.obj) Big a shout-out to [my brother](https://www.instagram.com/matalan09/?theme=dark) for designing these proposals.

## Steps
- Step 1
    - We have to remove the resistor (SB45) from the nucelo board, and move jumper (C20) to connect right and midle pin.
- Step 2
    - We will print the case. We will then install the display and encoder into it. As in the [photo](../../Photo/Photo_used_in_documentation/Photo_7.jpg). We will also install the conector on the adapter. As in the [photo](../../Photo/Photo_used_in_documentation/Photo_4.jpg). We then solder the cables to the display and the encoder. As in the [photo](../../Photo/Photo_used_in_documentation/Photo_6.jpg).
- Step 3
    - Now we will put the arduino CNC shield on the nucleo board. We will install 4 drivers into the CNC shield. As in the [photo](../../Photo/Photo_used_in_documentation/Photo_5.jpg).
- Step 4
    - We connect the display, encoder, 3V battery and power supply to the nucleo board. As in the [photo](../../Photo/Photo_used_in_documentation/Photo_8.png).
- Step 5
    - Now we will install the case on the wall and then connect the engines. As in the [photo](../../Photo/Photo_used_in_documentation/Connect_motor_CNC.png).

## Photo
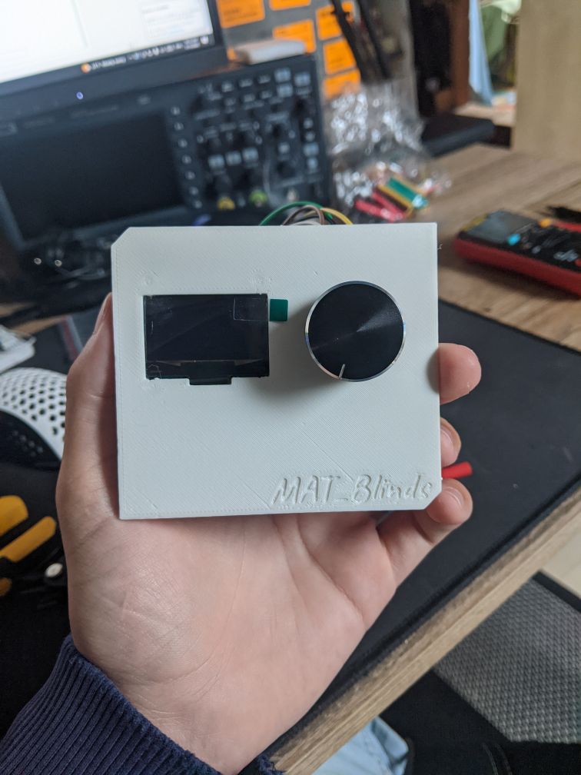
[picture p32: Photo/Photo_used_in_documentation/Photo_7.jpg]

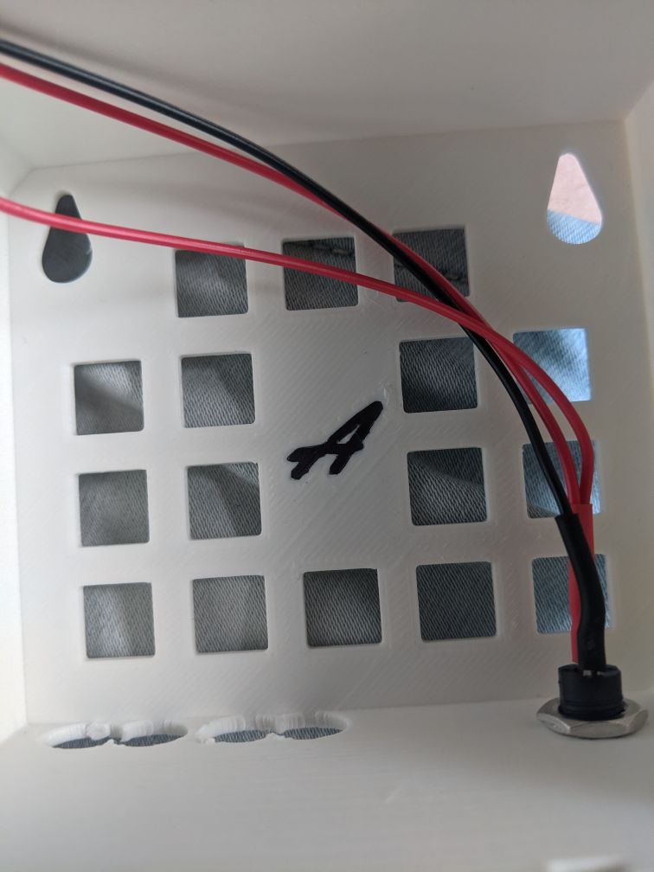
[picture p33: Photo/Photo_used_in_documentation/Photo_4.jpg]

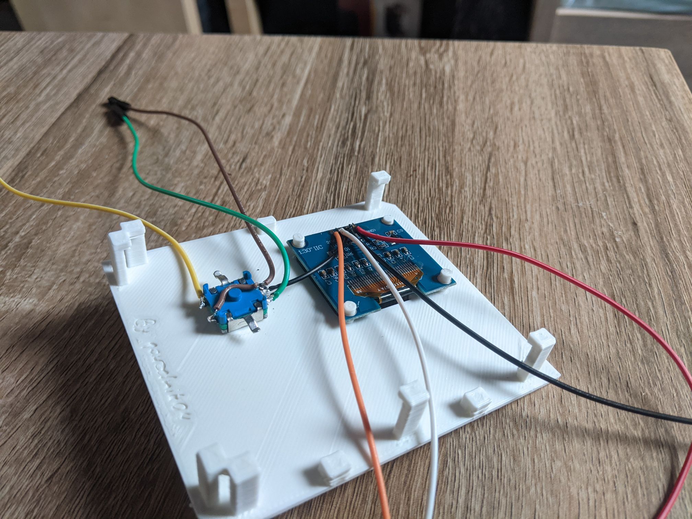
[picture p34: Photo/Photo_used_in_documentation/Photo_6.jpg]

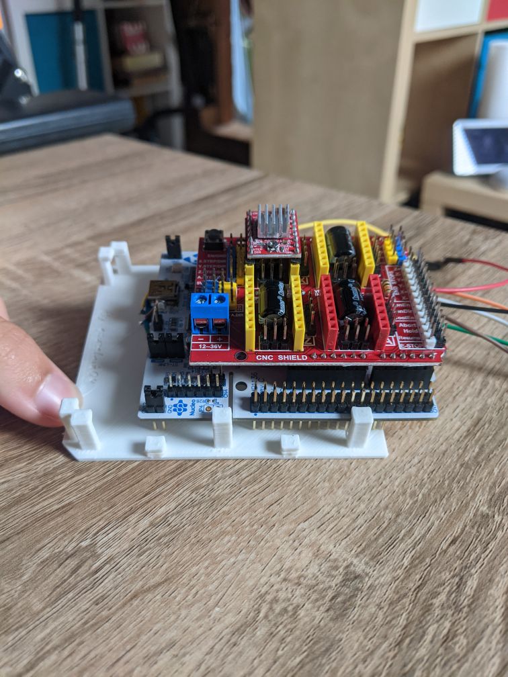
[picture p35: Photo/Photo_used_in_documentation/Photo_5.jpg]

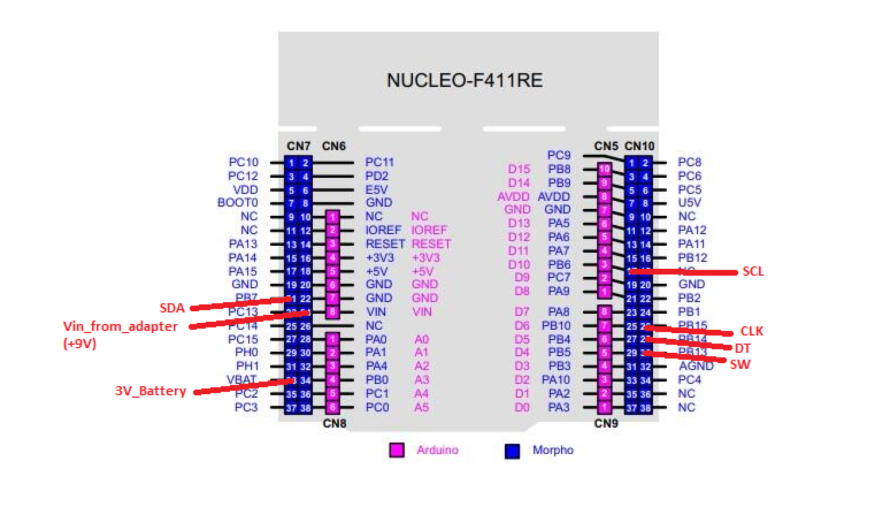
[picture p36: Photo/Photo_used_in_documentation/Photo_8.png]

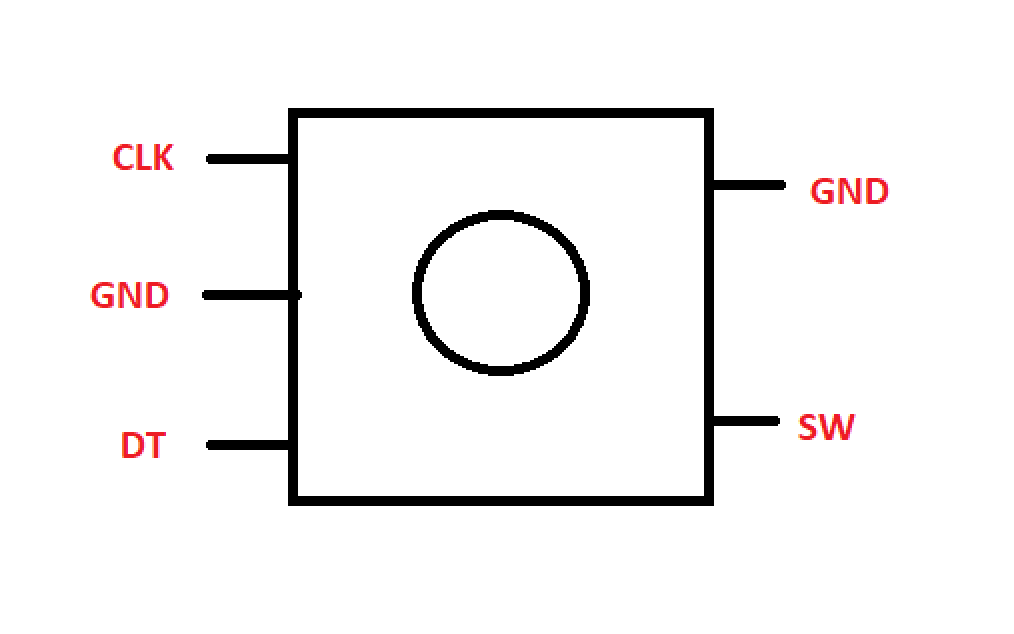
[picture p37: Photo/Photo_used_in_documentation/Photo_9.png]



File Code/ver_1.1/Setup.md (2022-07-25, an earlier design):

# Setup 

## Introduction
-   After the software is uploaded to the board, it still needs to be set up.

-   With ver_1.1 it is much more complicated. It will be necessary to start the STM32Cube, load the project ([MAT_Blinds_ver_1.1](MAT_Blinds_ver_1.1.zip)) into it and change the blind position values in "main.c". 
    - NOTE - Since this was my first major project in STM32cube and I didn't know how to use .c files, it will be necessary to [minimize the functions](../../Photo/Photo_used_in_documentation/main.c_3.png) in it after opening (Because all the functions are in "main.c".). Sorry for that ❤

- After opening, we find in the section "/* USER CODE BEGIN PV */" the values are set to 10,000. Now we have to pull the blinds up manually.

- Using debug and display, we will calibrate each blind separately. In the settings, we restart each blind. (Settings -> Calibration -> Calibration A) We do this with each blind.

- Now we press Window A -> extended -> extended. The blind should now move down, if it starts to move up, press the confirmation button again, it will immediately stop the blind. ([How to invert the movement of the blind](./invert_the_movement.md))

- If the blind goes down, when it reaches 1/3, we press the confirmation button and in the STM32 cube we find the current value of "window_A_1_3" using debug. We write this value instead of the value: "10,000".

- This is how we do it for all positions and all blinds.

- After that, we need to upload the new modified code to the board.

- Now we just have to set the time in the settings and when we want the blinds to pull up / pull down. 

### Photo
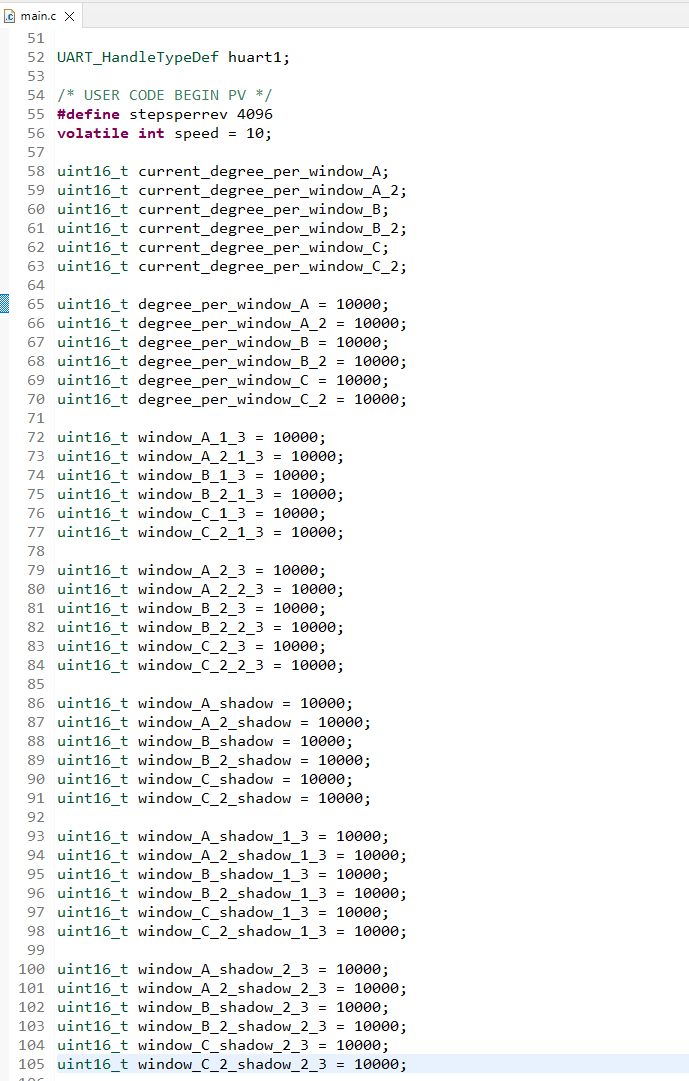
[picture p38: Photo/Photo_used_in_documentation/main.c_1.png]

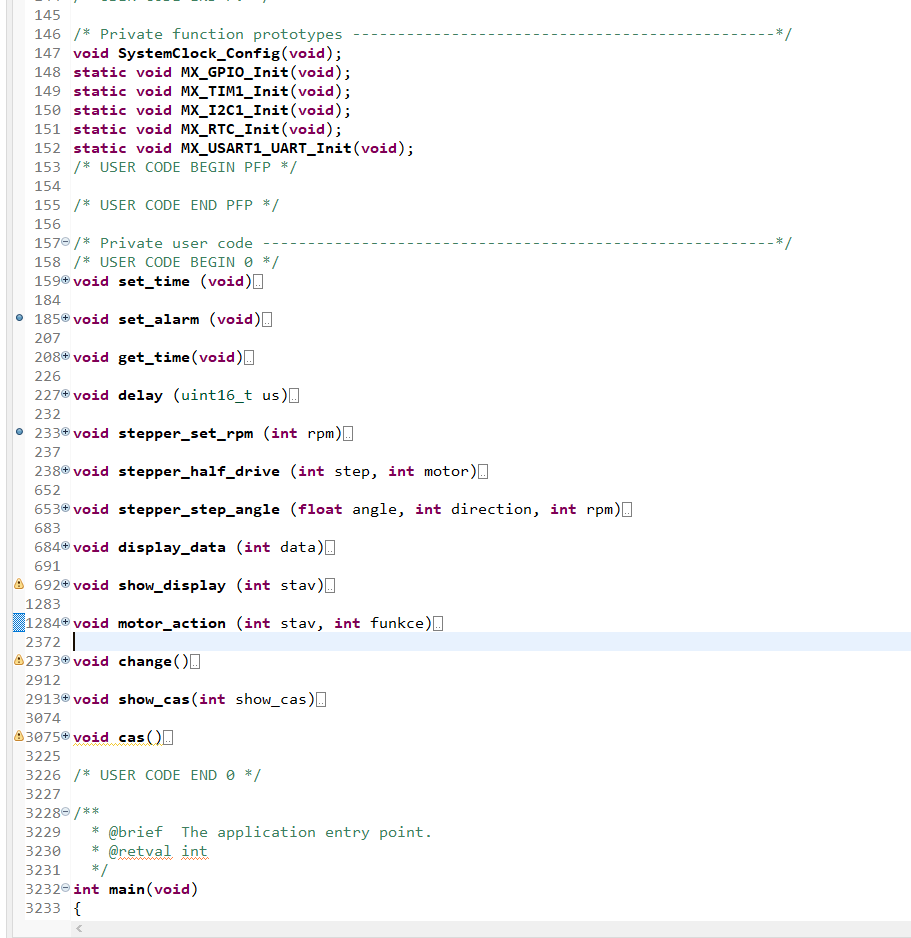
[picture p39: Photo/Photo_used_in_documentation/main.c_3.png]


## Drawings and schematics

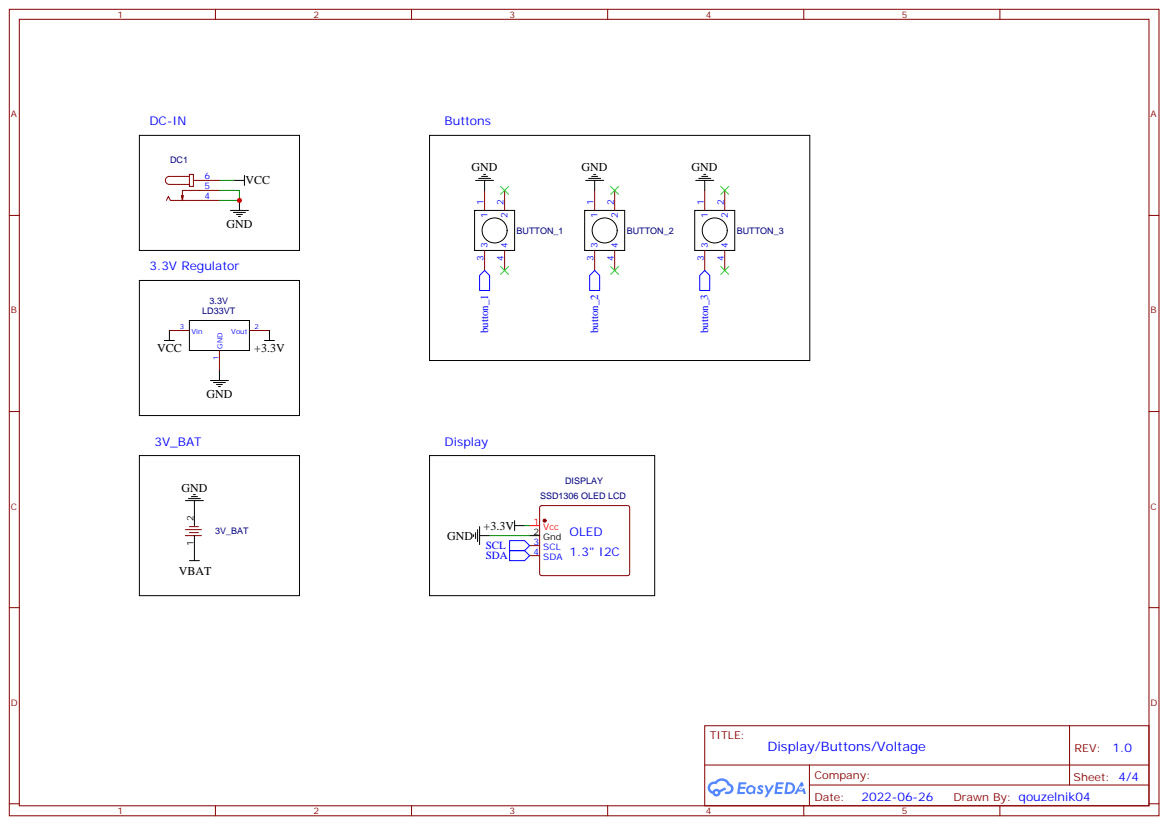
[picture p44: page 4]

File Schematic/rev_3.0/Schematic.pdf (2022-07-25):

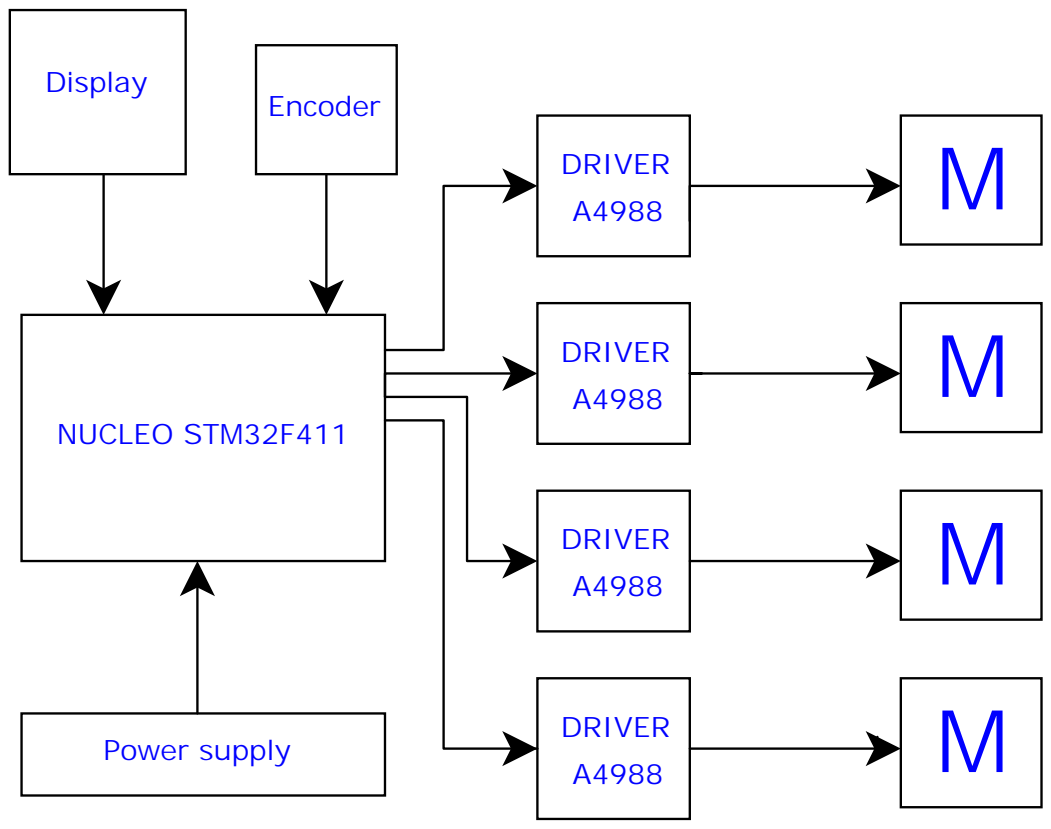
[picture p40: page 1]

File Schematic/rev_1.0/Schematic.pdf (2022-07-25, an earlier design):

M

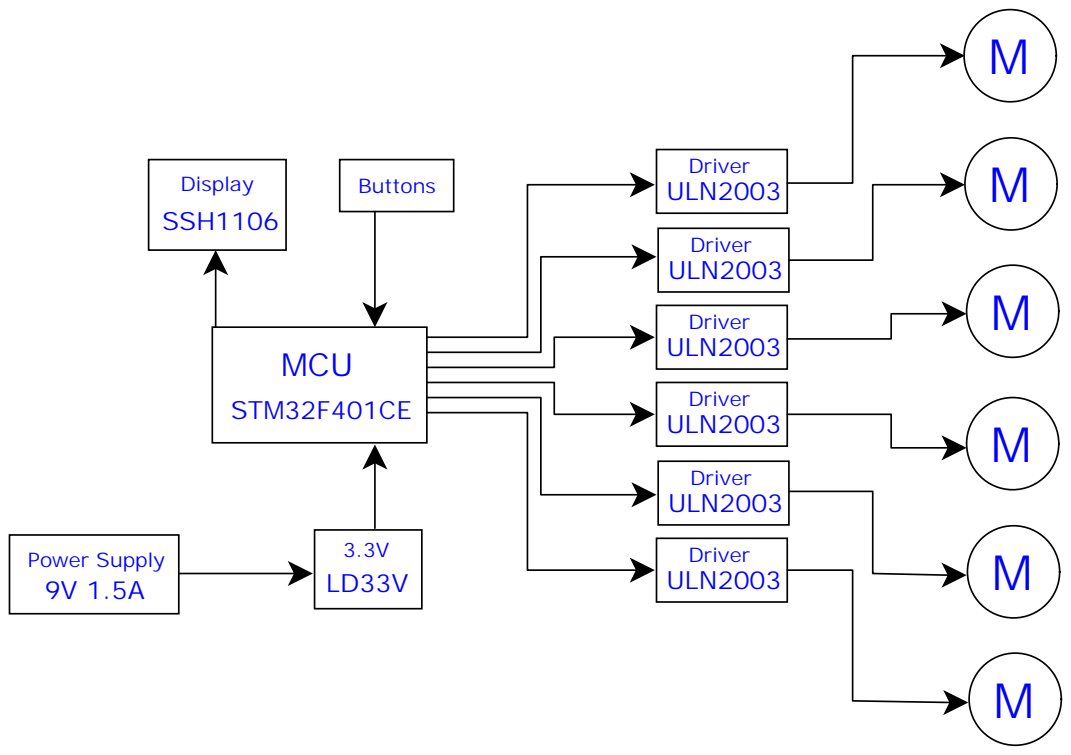
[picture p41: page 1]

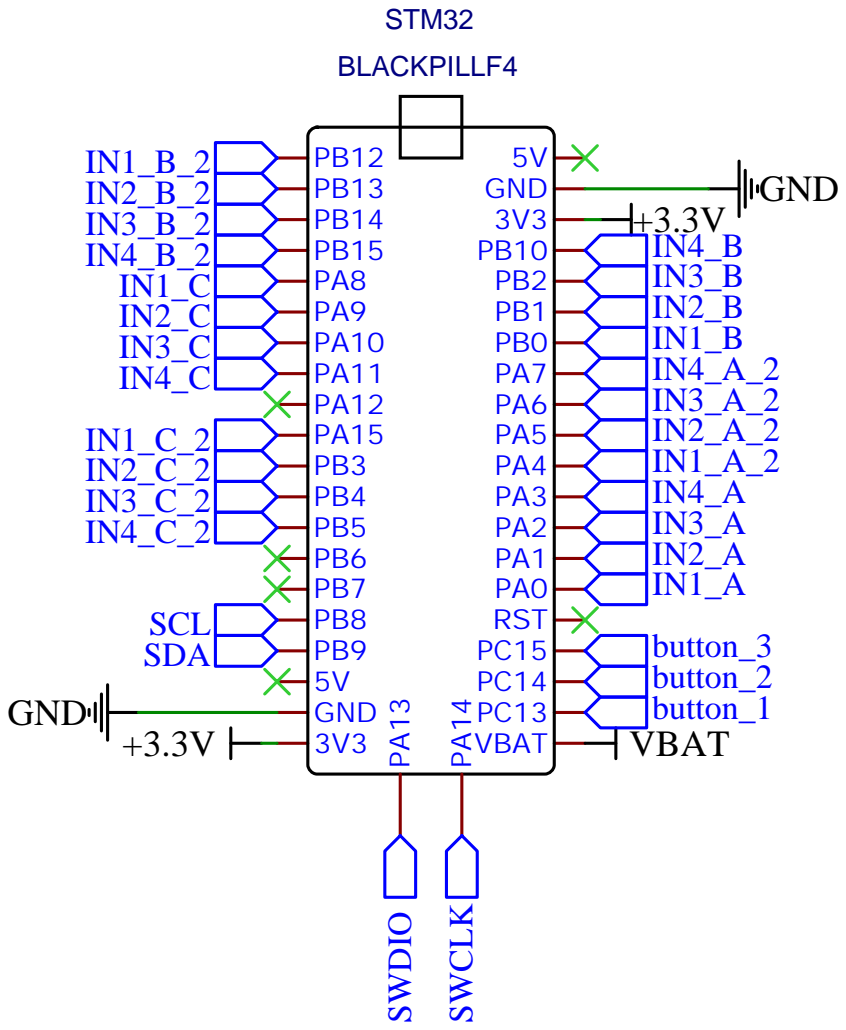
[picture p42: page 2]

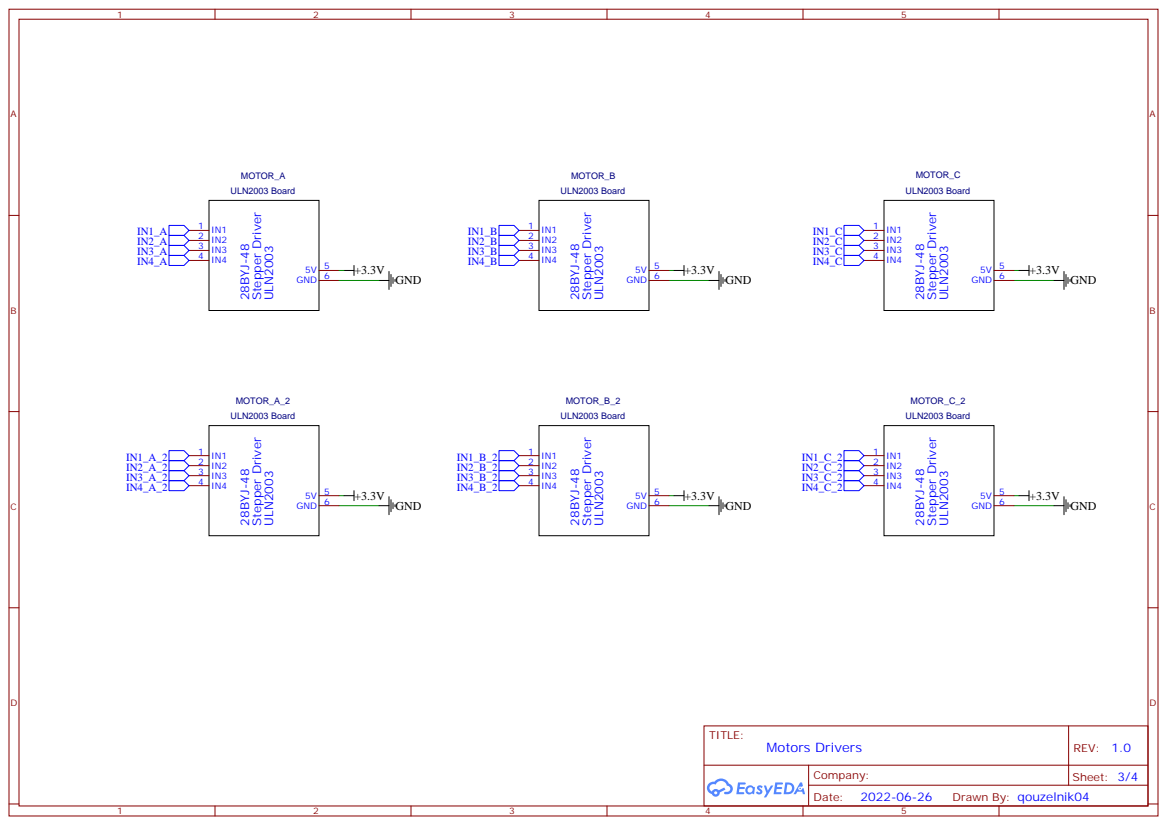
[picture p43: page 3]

## DC-IN

## Buttons
